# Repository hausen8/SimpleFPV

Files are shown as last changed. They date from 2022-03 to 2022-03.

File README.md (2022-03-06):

# SimpleFPV

If you need a low cost FPV drone that can be built by almost anyone, here it is.
This drone can be either 3D printed or simply cut from plywood. It was designed to carry a FPV camera and/or thermal camera like the FLIR Vue.

The drone can be equipped with almost any 7" or 8" motor/prop combination. If you have some old motors or ESCs, it is highly possible that you can use them. Flight controllers with a 30x30mm hole pattern are recommended but boxed controllers like the old DJI NAZA will fit, too. The battery size and voltage depends on the motors and motor controllers. Flight times up to 15 minutes with a lightweight cam are possible. Higher payload will reduce the flight time.

More information and documents will be added in the near future.

DIRECTORY                        | CONTENT
---------------------------------|----------------------------------------------------------
/3D-Print/                       | Directoy with all files for making the 3D printed version
/3D-Print/3D-Print_manual_XX.pdf | Manuals in different languages
/3D-Print/STL/                   | Sub directory containing all STL files
/3D-Print/3D-Print-N.png         | 3D Images of the drone
/Plywood/                        | Directoy with all files for making the plywood version
/Plywood/Plywood_manual_XX.pdf   | Manuals in different languages
/Plywood/Plywood-N.png           | 3D Images of the drone
/Plywood/Plywood-CNC.dxf         | CAD file for CNC milling or laser cutting the parts
/Plywood/Plywood-Parts.pdf       | PDF for printing contours on paper

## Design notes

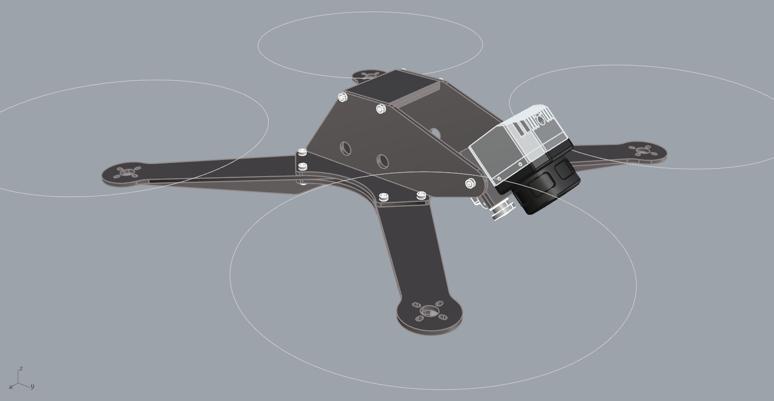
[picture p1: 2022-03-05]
Plywood/Plywood-1.png

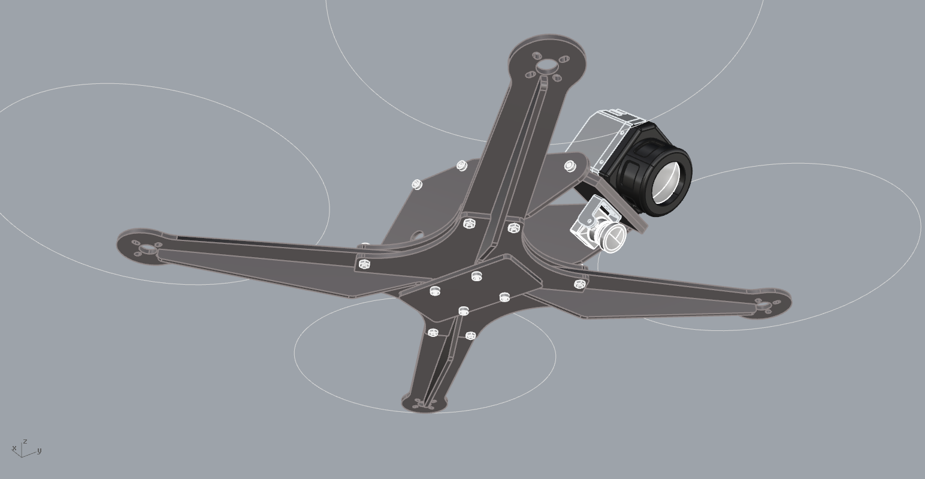
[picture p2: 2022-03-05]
Plywood/Plywood-2.png

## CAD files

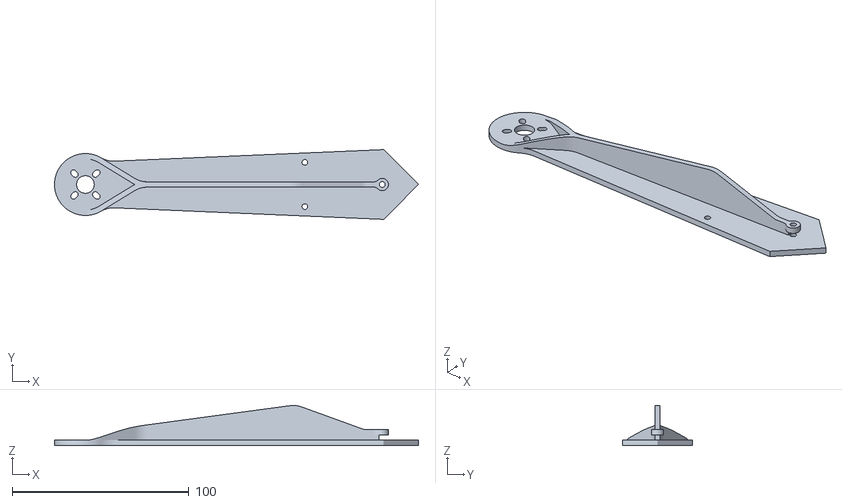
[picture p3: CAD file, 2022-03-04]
3D-Print/STL/Arm_2.stl
205.9 x 39.5 x 22.7

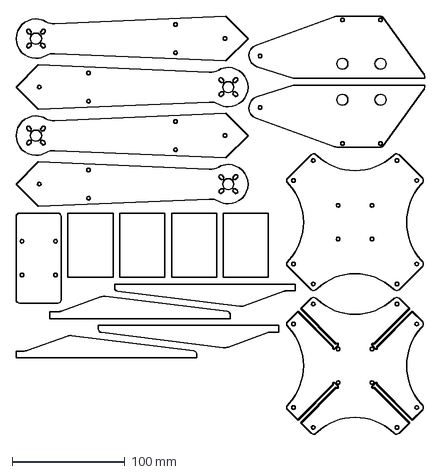
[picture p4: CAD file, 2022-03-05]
Plywood/Plywood-CNC.dxf
363.0 x 371.5 mm

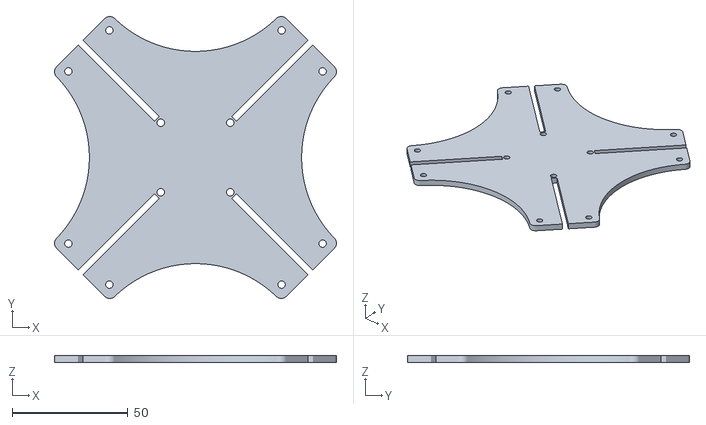
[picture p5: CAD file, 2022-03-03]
3D-Print/STL/CP_lower_2.stl
121.6 x 121.6 x 3.00

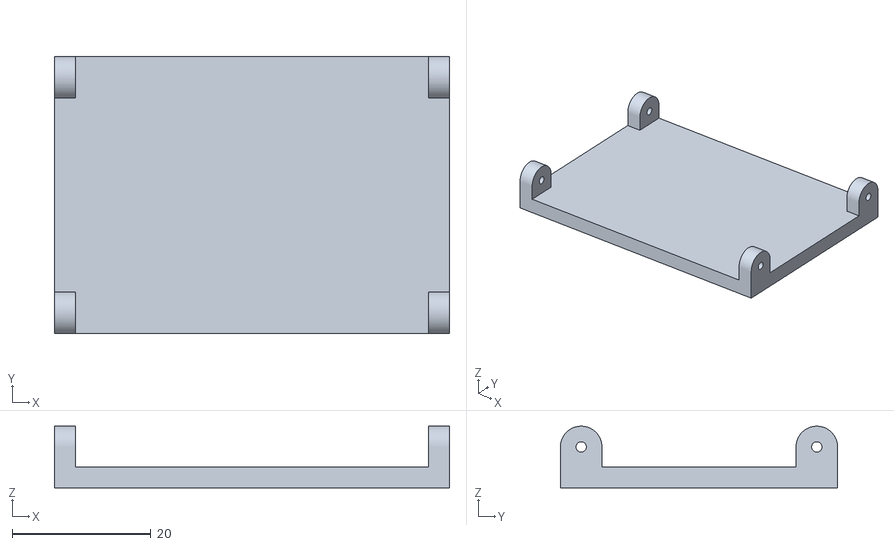
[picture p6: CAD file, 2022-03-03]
3D-Print/STL/VTX_plate.stl
57.0 x 40.0 x 8.90

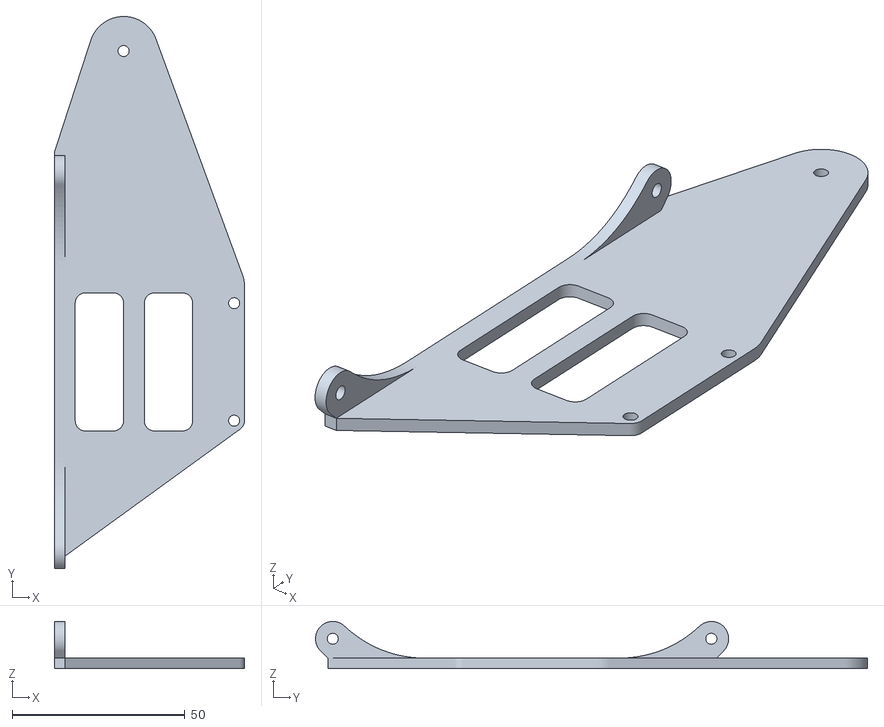
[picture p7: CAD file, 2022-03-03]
3D-Print/STL/Side_L.stl
55.0 x 159.8 x 13.6

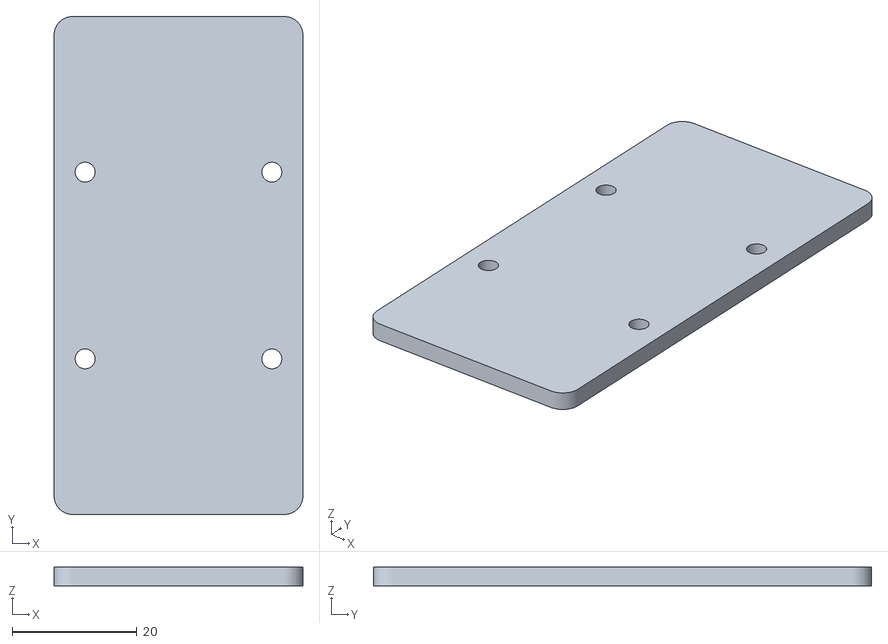
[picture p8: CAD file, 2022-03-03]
3D-Print/STL/BAT_plate.stl
40.0 x 80.0 x 3.00

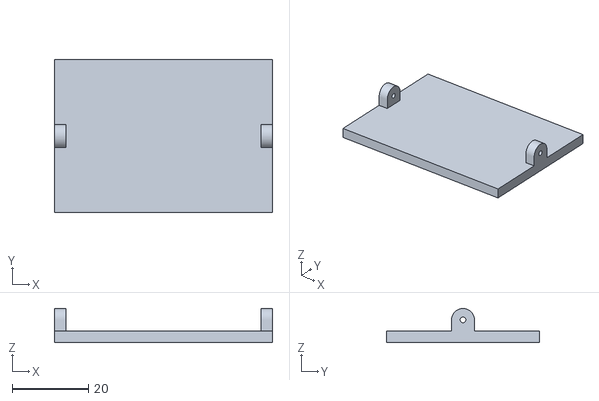
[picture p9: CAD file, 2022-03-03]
3D-Print/STL/CAM_plate.stl
57.0 x 40.0 x 8.90

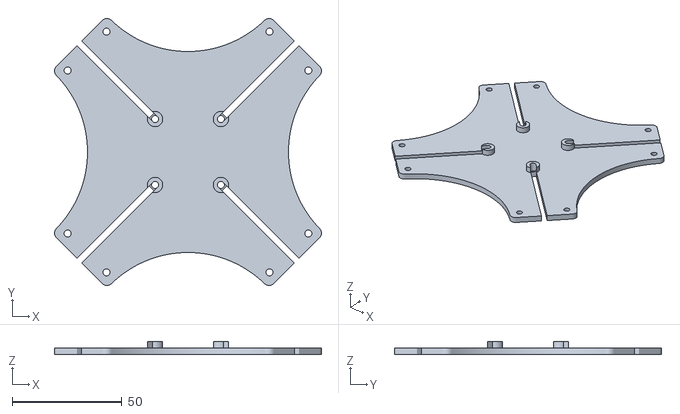
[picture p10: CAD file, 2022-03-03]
3D-Print/STL/CP_lower.stl
121.6 x 121.6 x 6.00

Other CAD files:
3D-Print/STL/Arm.stl
3D-Print/STL/Side_R.stl
3D-Print/STL/CP_upper.stl

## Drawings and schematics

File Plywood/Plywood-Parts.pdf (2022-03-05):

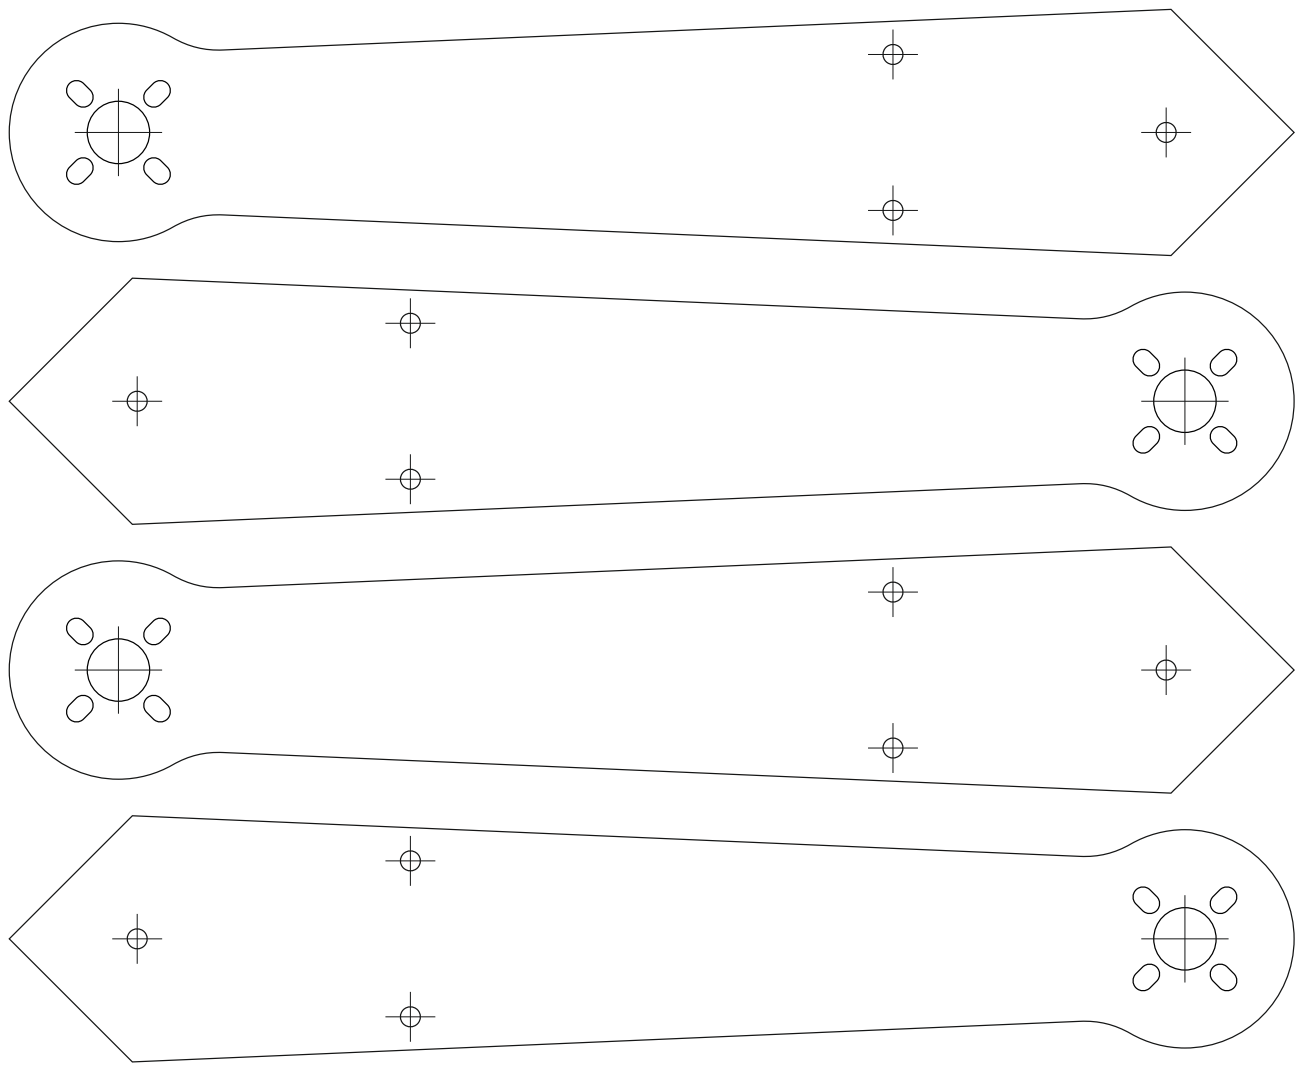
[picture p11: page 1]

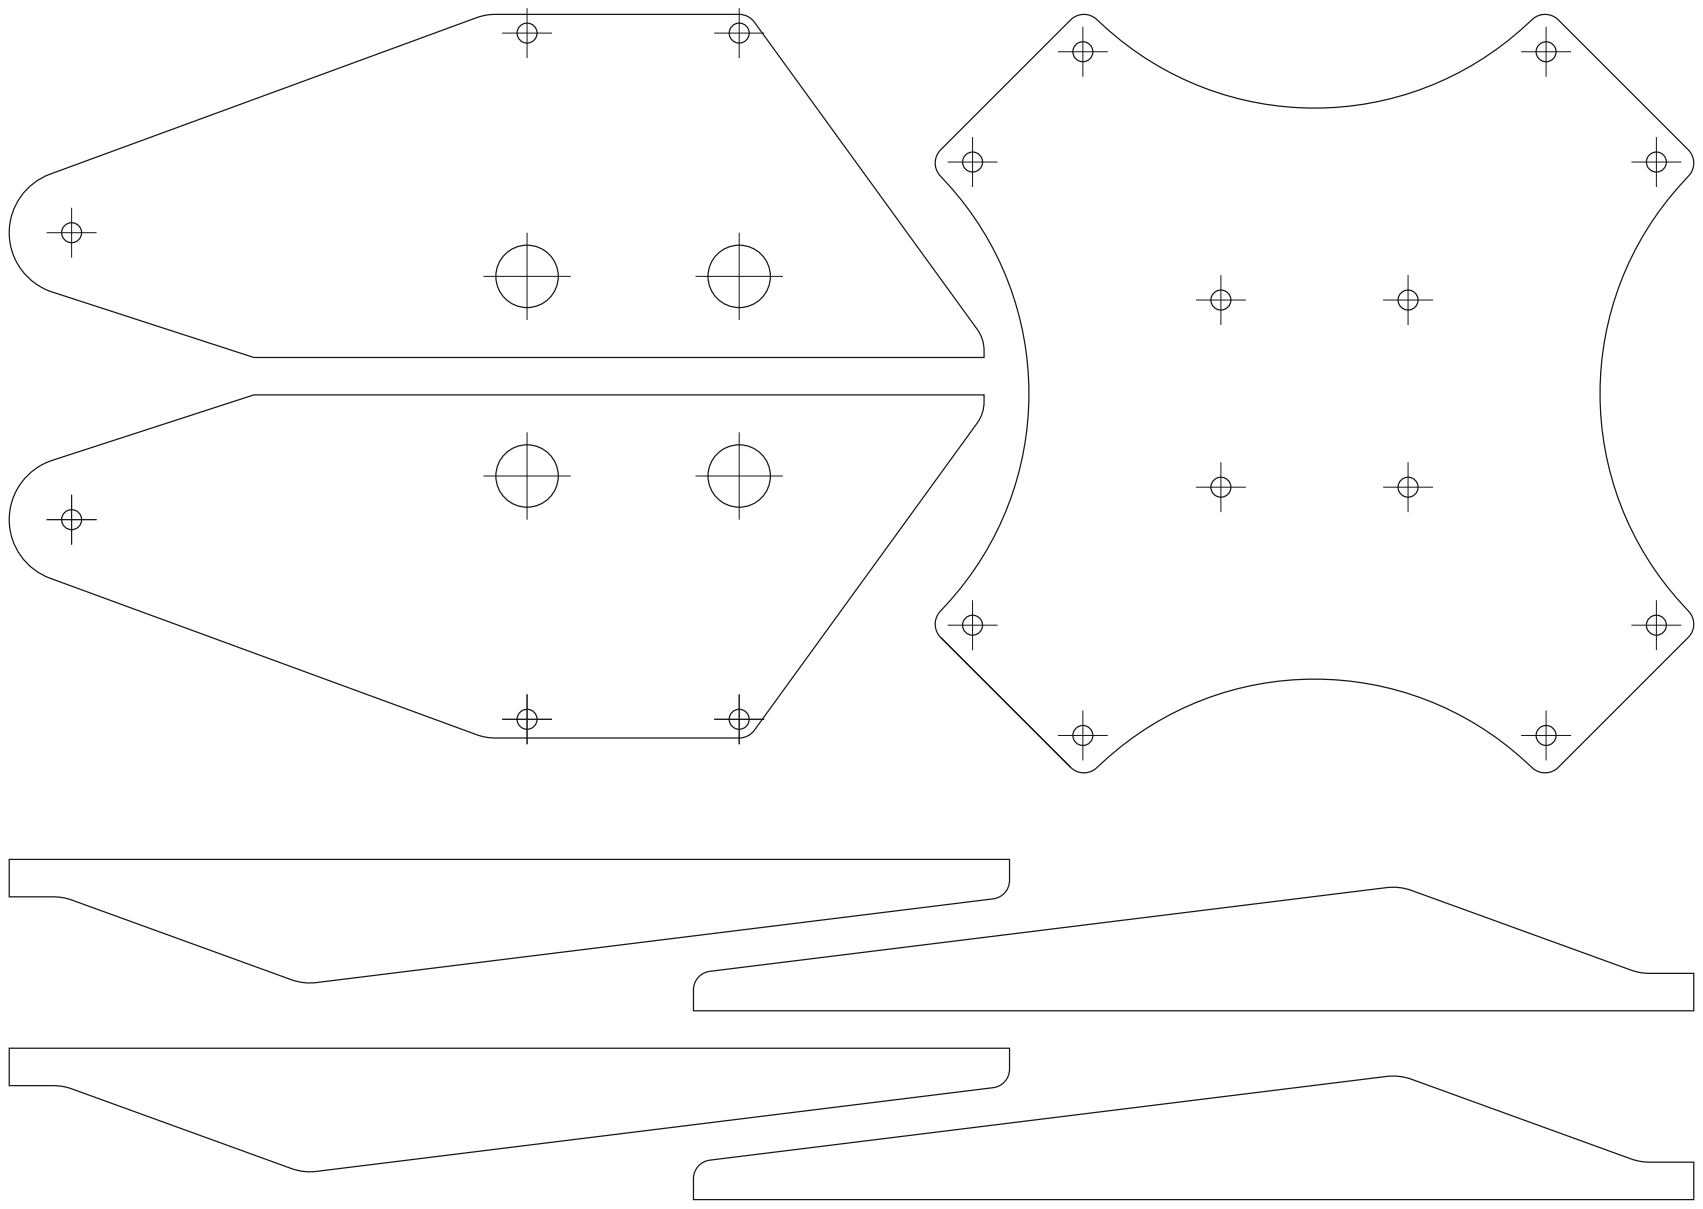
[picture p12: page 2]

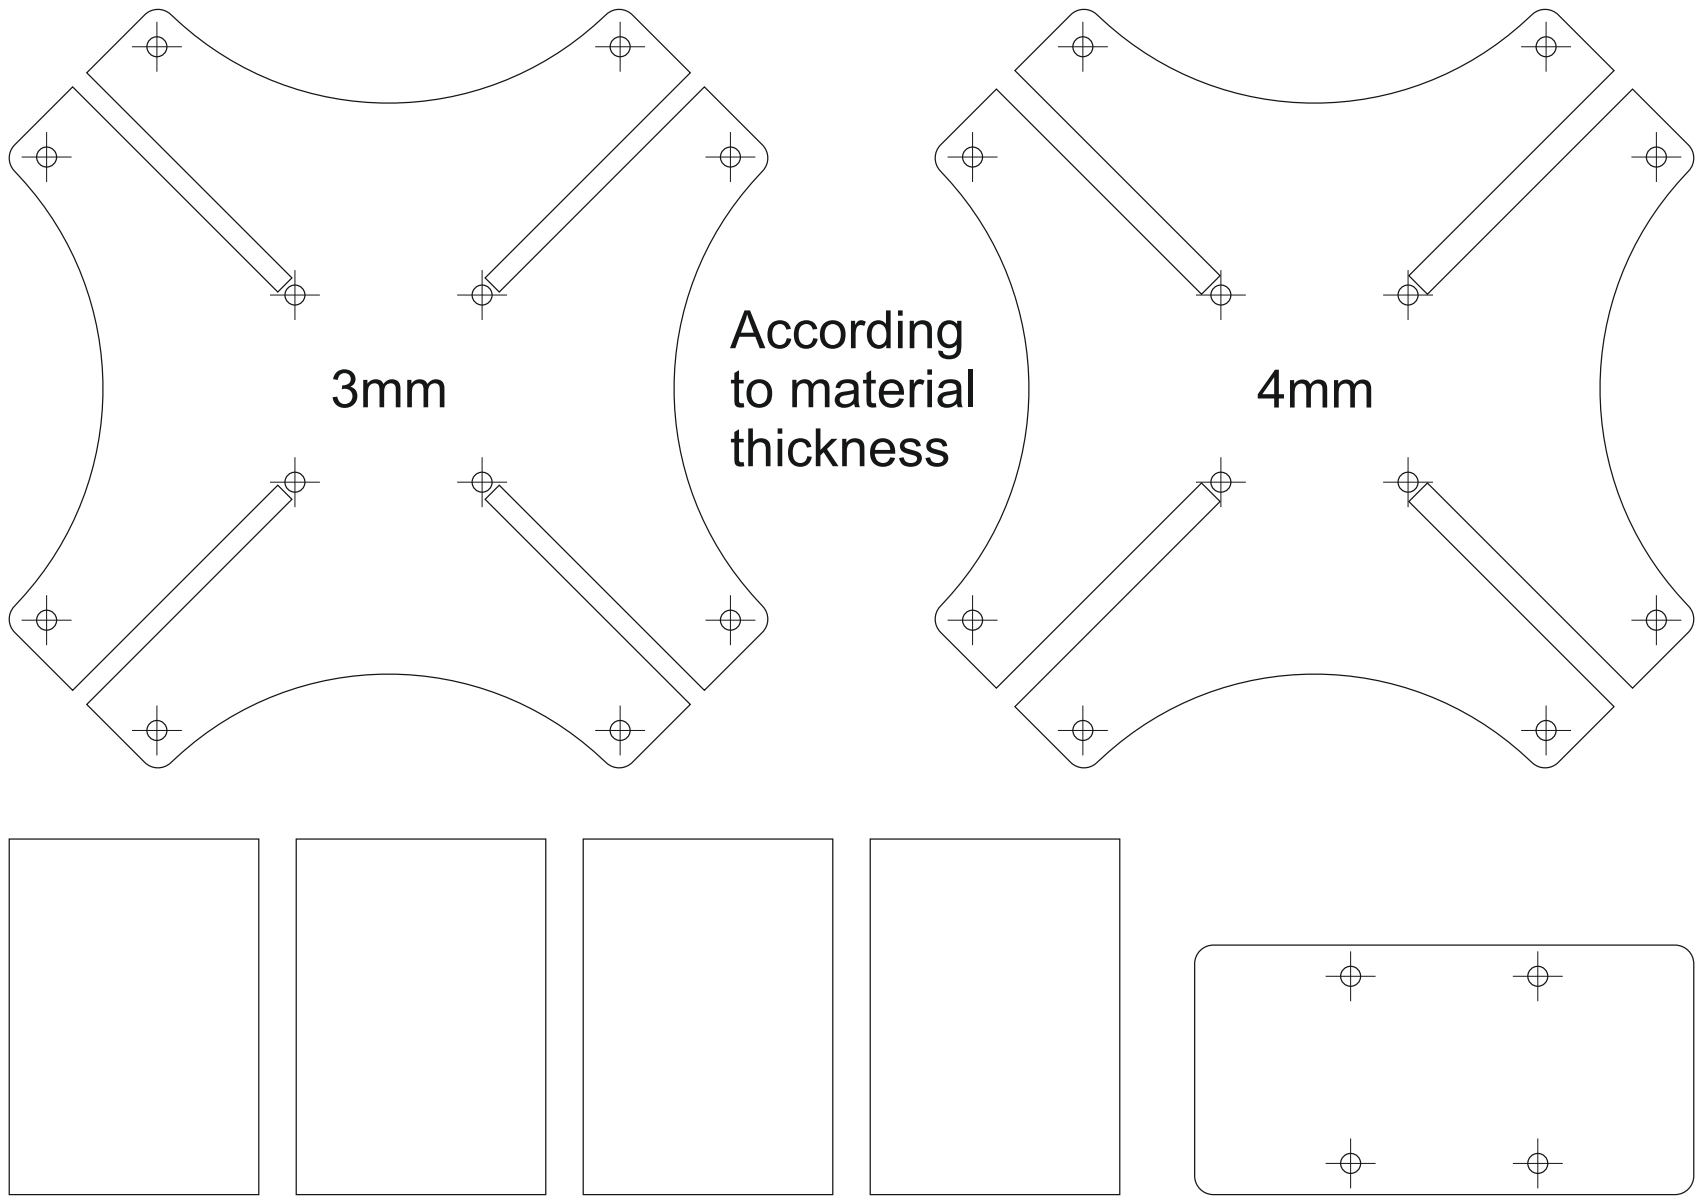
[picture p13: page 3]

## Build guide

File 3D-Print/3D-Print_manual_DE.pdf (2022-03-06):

3D-Druck:

Druck mit PLA: Top and bottom solid layers: 3, Outlines: 3, Infill honeycomb 20%
Bei den STL-Dateien besteht die Wahl zwischen zwei verschiedenen Armen:
- Arm_1.stl lässt sich wie alle anderen Teile ohne Support drucken, ergibt aber einen weniger steifen Rahmen. Diese Variante wird empfohlen, wenn keine besonderen Erfahrungen im 3D-Druck vorhanden sind.
- Arm_2.stl muss mit Support an der überhängenden Schraubenöse gedruckt werden. Nach dem Druck wird der Support entfernt. Diese Konstruktion führt zu einem steiferen Rahmen und richtet sich an erfahrenere Anwender.

Achtung: Zu jedem Arm gehört eine entsprechende untere Centerplate. Arm_1.stl ist nicht mit CP_lower_2.stl kompatibel und umgekehrt.

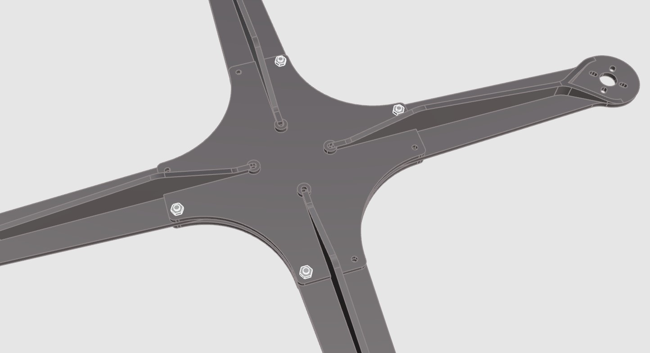
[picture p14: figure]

Schritt 1 (Arm_1):

Alle vier Arme mit je einer M3x15 Schraube an zwei gegenüberliegenden Seiten der oberen Centerplate fixieren. Anschließend die untere Centerplate auflegen und mit vier Muttern sichern.

Schritt 1 (Arm_2):

Einen Arm nach dem anderen zwischen die Centerplates schieben und mit je einer M3x15 Schraube und Mutter an zwei gegenüberliegenden Seiten sichern.

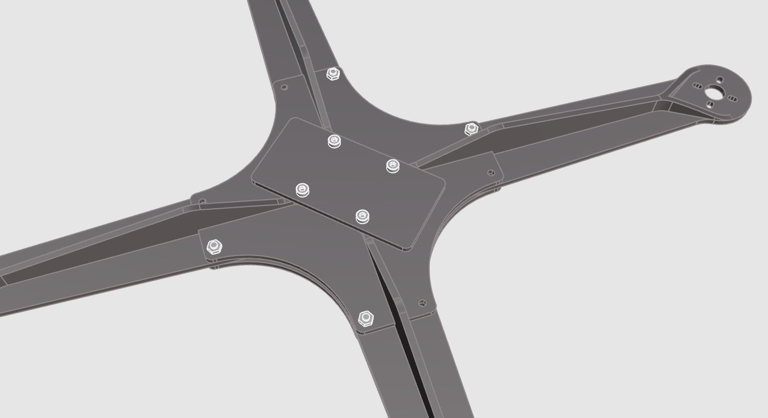
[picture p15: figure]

Schritt 2:

Den Akkuträger mit vier Schrauben M3x20 aufsetzen.

Schritt 3:

Auf der Gegenseite vier M3 Distanzbolzen auf die Schrauben aufsetzen und festziehen. Für die Elektronik steht eine Gesamthöhe von 49 Millimetern zur Verfügung. Bei mehreren elektronischen Boards sollten entsprechend kurze Distanzbolzen gewählt werden.

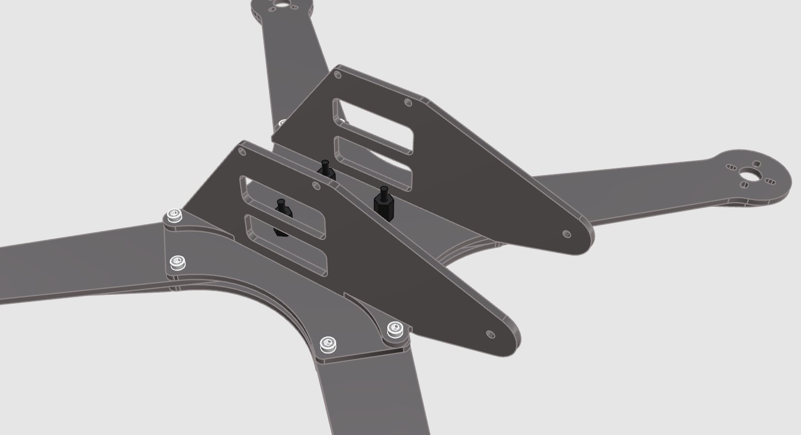
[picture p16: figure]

Schritt 4:

Seitenteile mit jeweils zwei M3x15 aufsetzen und auf der Rückseite mit Muttern sichern.

Schritt 5:

Die obere Trägerplatte kann wahlweise mit M3 Schrauben und Muttern oder aber mit Treibschrauben befestigt werden. Um M3 Schrauben zu verwenden, müssen die Bohrungen an der Trägerplatte auf 3mm aufgebohrt werden. Treibschrauben mit 2mm bis 2,6mm Durchmesser können ohne Aufbohren eingesetzt werden und schneiden sich ihr Gewinde selbst.

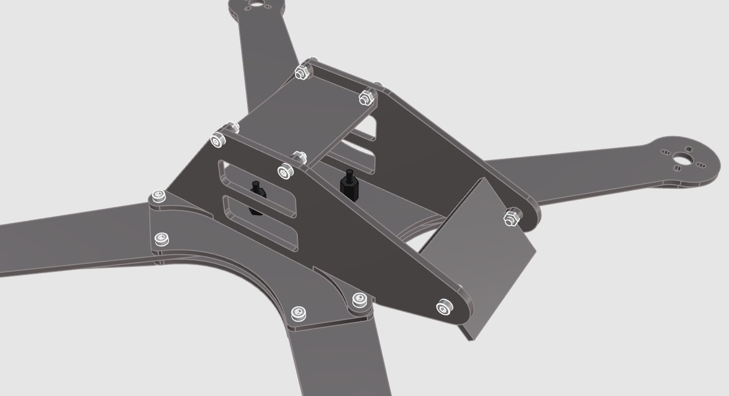
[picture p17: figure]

Schritt 6:

Auch die Trägerplatte für die Kameras kann wahlweise mit M3 Schrauben und Muttern oder mit Treibschrauben befestigt werden. Bei der Verwendung von M3 Schrauben müssen die Bohrungen des Trägers ebenfalls auf 3mm aufgebohrt werden. In diesem Fall sind Sicherungsmuttern empfohlen, damit sich der Träger mit der Kamera nicht während des Fluges verstellt.

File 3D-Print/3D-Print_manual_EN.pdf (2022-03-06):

3D Print:

Print with PLA: Top and bottom solid layers: 3, Outlines: 3, Infill honeycomb 20%
With the STL files there is a choice between two different arms:
- Arm_1.stl can be printed without support like all other parts, but results in a less rigid frame. This variant is recommended if you do not have any special experience in 3D printing.
- Arm_2.stl must be printed with support on the overhanging screw eyelet. After printing, the support is removed. This construction results in a stiffer frame and is aimed at more experienced users.

Note: Each arm has a corresponding lower center plate. Arm_1.stl is not compatible with CP_lower_2.stl and vice versa.


Step 1 (Arm_1):

Fix all four arms with one M3x15 screw each on two opposite sides of the upper center plate. Then place the lower center plate and secure with four nuts.

Step 1 (Arm_2):

Slide one arm at a time between the center plates and secure with an M3x15 screw and nut on two opposite sides.


Step 2:

Attach the battery carrier with four screws M3x20.

Step 3:

Place four M3 spacer bolts on the screws on the opposite side and tighten. A total height of 49 millimeters is available for the electronics. If there are several electronic boards, correspondingly short spacer bolts should be selected.


Step 4:

Put on the side parts with two M3x15 each and secure them with nuts on the back.

Step 5:

The upper support plate can be attached either with M3 screws and nuts or with self-tapping screws. In order to use M3 screws, the holes on the carrier plate must be drilled out to 3mm. Self-tapping screws with a diameter of 2mm to 2.6mm can be used without drilling and tap their own thread.


Step 6:

The support plate for the cameras can also be attached either with M3 screws and nuts or with self-tapping screws. When using M3 screws, the holes in the carrier must also be drilled out to 3mm. In this case, locking nuts are recommended to prevent the carrier with the camera from moving during flight.

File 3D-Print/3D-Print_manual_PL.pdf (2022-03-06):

Drukowanie 3D:

Drukowanie z PLA: Top and bottom solid layers: 3, Outlines: 3, Infill honeycomb 20%
W przypadku pilników STL mamy do wyboru dwa różne ramiona:
- Arm_1.stl można wydrukować bez wsparcia, jak wszystkie inne części, ale daje mniej sztywną ramkę. Ten wariant jest zalecany, jeśli nie masz specjalnego doświadczenia w druku 3D.
- Arm_2.stl musi być wydrukowany z podporą na zwisającym oczku śruby. Po wydrukowaniu podpora jest usuwana. Taka konstrukcja skutkuje sztywniejszą ramą i jest skierowana do bardziej doświadczonych użytkowników.

Uwaga: Każde ramię ma odpowiednią dolną płytę środkową. Arm_1.stl nie jest kompatybilny z CP_lower_2.stl i na odwrót.


Krok 1 (Ramię_1):

Zamocuj wszystkie cztery ramiona za pomocą jednej śruby M3x15 po dwóch przeciwnych stronach górnej płyty środkowej. Następnie umieść dolną płytę środkową i zabezpiecz czterema nakrętkami.

Krok 1 (Ramię_2):

Wsuń jedno ramię na raz między płyty środkowe i zabezpiecz śrubą M3x15 i nakrętką po dwóch przeciwnych stronach.


Krok 2:

Przymocuj nośnik baterii czterema śrubami M3x20.

Krok 3:

Umieść cztery śruby dystansowe M3 na śrubach po przeciwnej stronie i dokręć. Dla elektroniki dostępna jest całkowita wysokość 49 milimetrów. Z kilkoma elektronicznymi deskimi należy dobrać odpowiednie śruby dystansowe.


Krok 4:

Załóż boczne części po dwa M3x15 każda i zabezpiecz je nakrętkami z tyłu.

Krok 5:

Górną płytę nośną można przymocować za pomocą śrub i nakrętek M3 lub za pomocą wkrętów samogwintujących. Aby użyć śrub M3, otwory w płycie nośnej muszą być wywiercone do 3mm. Wkręty samogwintujące o średnicy od 2mm do 2,6mm można stosować bez wiercenia i gwintowania własnym gwintem.


Krok 6:

Płytę nośną dla kamer można również przymocować za pomocą śrub i nakrętek M3 lub wkrętów samogwintujących. W przypadku użycia śrub M3 otwory w nośniku muszą być również wywiercone do 3 mm. W takim przypadku zalecane są nakrętki blokujące, aby zapobiec przesuwaniu się nośnika z kamerą podczas lotu.

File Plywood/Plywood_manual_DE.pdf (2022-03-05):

Aussägen der Teile per Hand:

Drucke die Datei Plywood-Parts.pdf aus und klebe das Papier auf 4mm Sperrholz. Zur Not geht auch 3mm Sperrholz. Säge anschließend die Umrisse aus dem Sperrholz aus. Die untere Centerplate ist das einzige Teil, das sich nach Materialstärke unterscheidet. Es ist an den meisten Stellen keine besondere Präzision nötig. Auch die abgerundeten Ecken sind nicht wichtig.

CNC-gesteuertes Fräsen oder Laserschneiden:

Lade die Datei Plywood-CNC.dxf. Die Innen- und Außenkonturen sind jeweils auf einer eigenen Ebene abgelegt. Da sich die untere Centerplate für 3mm- oder 4mm-Sperrholz leicht unterscheidet, ist zu den Außenkonturen die Ebene mit der entsprechenden Centerplate auszuwählen.

Montage:

Die Arme können mit den beiden Centerplates wahlweise verschraubt oder verleimt werden. Eine Verleimung führt zu höherer Stabilität, verhindert aber die Möglichkeit einer späteren Reparatur. Wenn die Centerplates mit den Armen verleimt werden sollen, müssen die äußeren Schraubenlochpaare nicht gebohrt werden. Die inneren vier Bohrungen im 30x30mm Raster müssen in jedem Fall gebohrt werden.

Ein paar Bohrungen in den Seitenteilen des Aufbaus werden die spätere Verkabelung erleichtern.

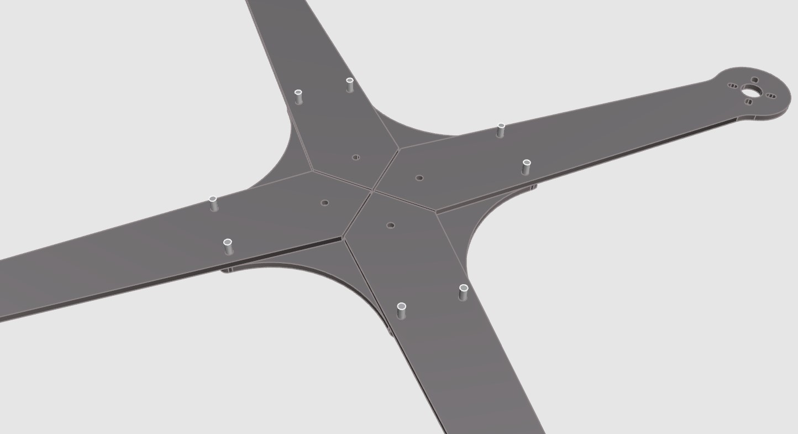
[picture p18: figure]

Schritt 1:

An den äußeren Enden M3x15 Schrauben durch die obere Centerplate und die vier Arme stecken. Alternativ können die Arme auch mit der Centerplate verleimt werden. Zwischen den Armen sollte ein Spalt von 1 Millimeter verbleiben.

Schritt 2:

Die untere Centerplate auflegen und mit M3 Muttern verschrauben. Zur besseren Ausrichtung sollten durch die vier inneren Bohrungen Schrauben gesteckt werden. Alternativ zur Verschraubung kann auch die untere Centerplate verleimt werden.

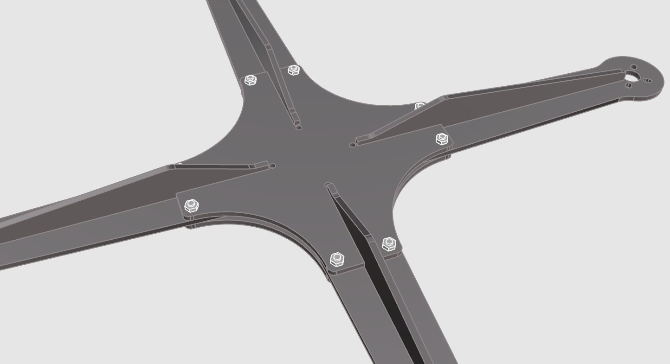
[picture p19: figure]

Schritt 3:

Die Schlitze der unteren Centerplate mit etwas Leim füllen. Die Auflageflächen der Versteifungen ebenfalls mit Leim bestreichen und auf die Arme aufleimen. Die Versteifungen dabei bis zum Anschlag in die Schlitze der unteren Centerplate drücken.

Schritt 4:

Akkuträger mit vier Schrauben M3x20 aufsetzen. Zur besseren Stabilität können die Auflageflächen auf den Versteifungen der Arme mit Leim bestrichen werden.

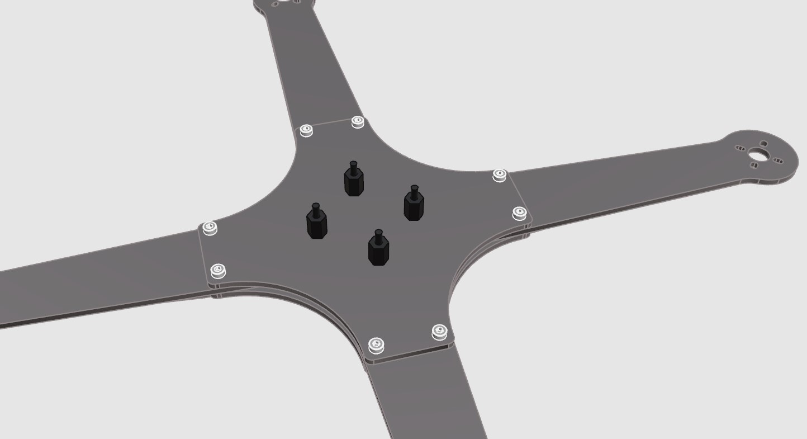
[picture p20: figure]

Schritt 5:

Auf der Gegenseite vier M3 Distanzbolzen auf die Schrauben aufsetzen und festziehen. Für die Elektronik steht eine Gesamthöhe von 49 Millimetern zur Verfügung. Bei mehreren elektronischen Boards sollten entsprechend kurze Distanzbolzen gewählt werden.

Schritt 6:

Zwei der vier 40x57mm Trägerplatten zusammenleimen und mit den beiden Seitenteilen verschrauben. Zum Verschrauben eignen sich Holzschrauben bis ca. 3mm, wobei zur Sicherheit vorgebohrt werden sollte. Ein Verleimen der Trägerplatte mit den Seitenteilen ist nicht empfehlenswert, da dadurch die Montage der Elektronik erschwert wird. Anschließend den Aufbau mit ausreichend Leim auf den Kontaktflächen auf die obere Centerplate aufsetzen und gerade in Flugrichtung ausrichten.

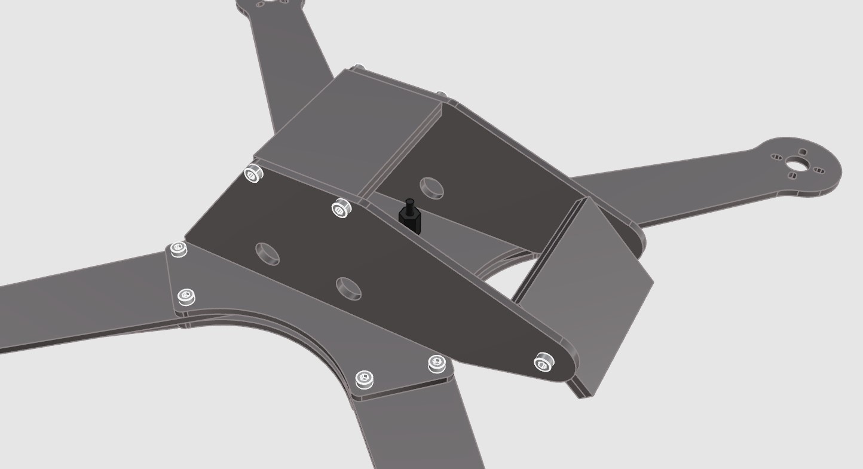
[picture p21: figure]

Schritt 7:

Die anderen beiden Trägerplatten ebenfalls miteinander verleimen. An den 40mm langen Kanten jeweils den Mittelpunkt markieren und vor dem Verschrauben vorbohren.

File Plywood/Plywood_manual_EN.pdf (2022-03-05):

Sawing out the parts by hand:

Print out the Plywood-Parts.pdf file and glue the paper onto 4mm plywood. In a pinch, 3mm plywood will do. Then saw the outlines out of the plywood. The lower center plate is the only part that differs in material thickness. No particular precision is required in most places. The rounded corners are also not important.

CNC controlled milling or laser cutting:

Load the Plywood-CNC.dxf file. The inner and outer contours are each stored on a separate layer. Since the lower center plate differs slightly for 3mm or 4mm plywood, the level with the corresponding center plate must be selected together with the outer contours.

Assembly:

The arms can either be screwed or glued to the two center plates. Gluing leads to greater stability, but prevents the possibility of later repairs. If the center plates are to be glued to the arms, the outer pairs of screw holes do not have to be drilled. The inner four holes in the 30x30mm grid must be drilled in any case.

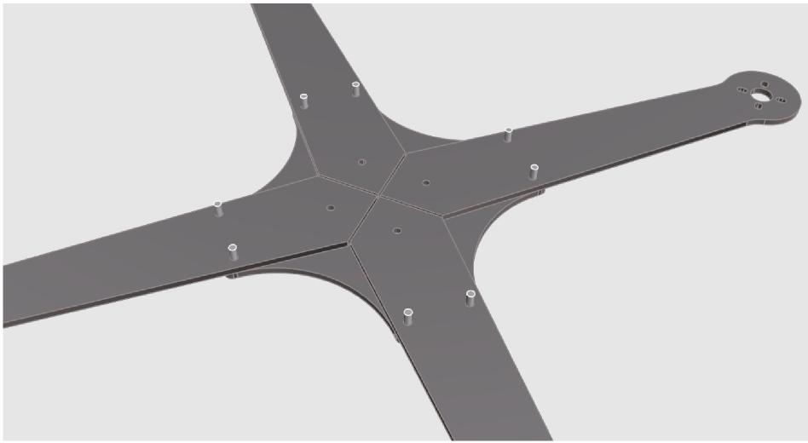
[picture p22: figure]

Step 1:

At the outer ends, insert M3x15 screws through the upper center plate and the four arms. Alternatively, the arms can also be glued to the center plate. A gap of 1 millimeter should remain between the arms.

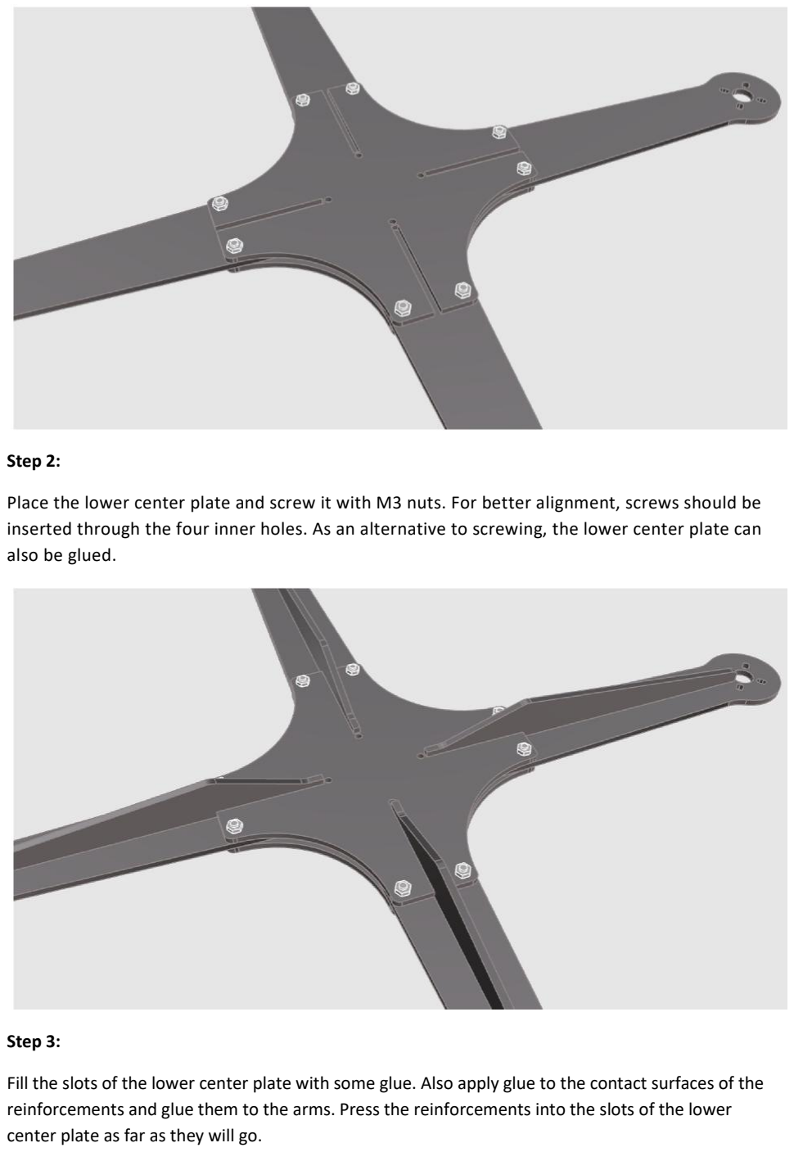
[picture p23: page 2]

Step 2:

Place the lower center plate and screw it with M3 nuts. For better alignment, screws should be inserted through the four inner holes. As an alternative to screwing, the lower center plate can also be glued.

Step 3:

Fill the slots of the lower center plate with some glue. Also apply glue to the contact surfaces of the reinforcements and glue them to the arms. Press the reinforcements into the slots of the lower center plate as far as they will go.

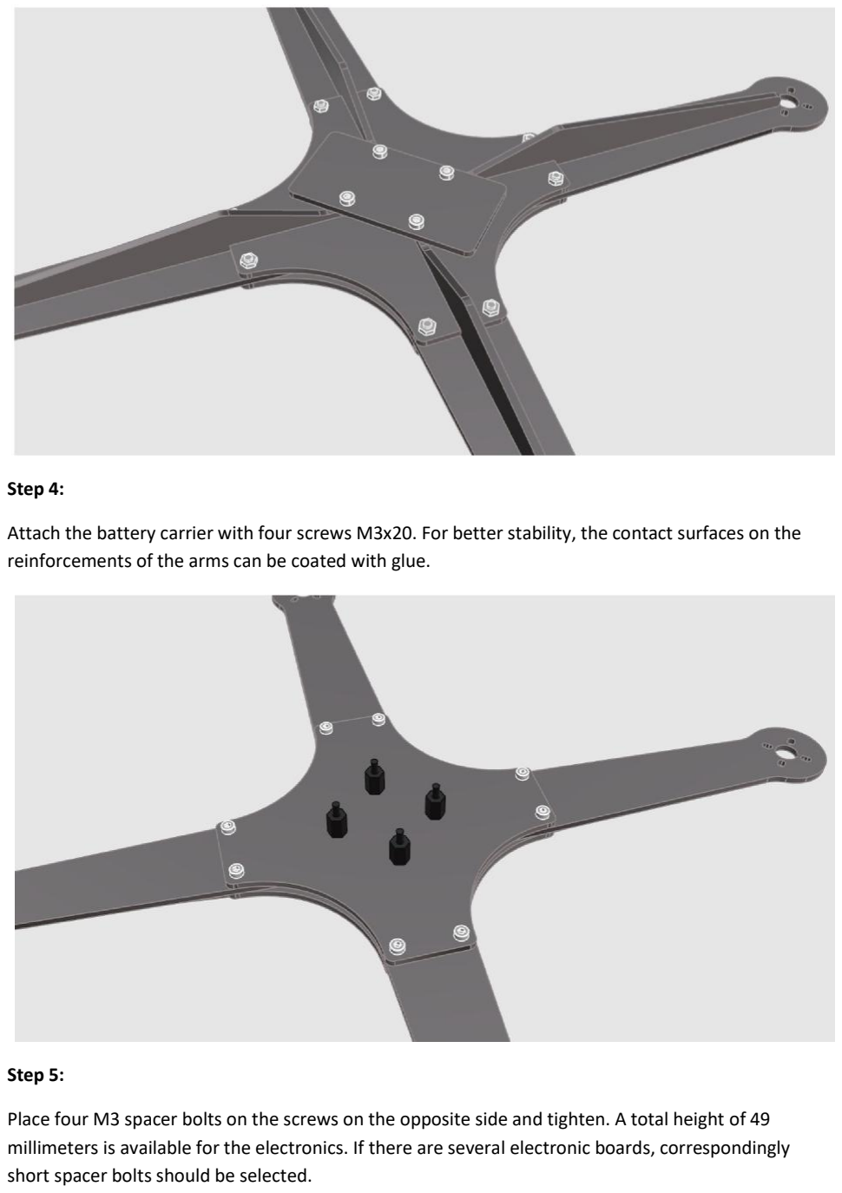
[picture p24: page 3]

Step 4:

Attach the battery carrier with four screws M3x20. For better stability, the contact surfaces on the reinforcements of the arms can be coated with glue.

Step 5:

Place four M3 spacer bolts on the screws on the opposite side and tighten. A total height of 49 millimeters is available for the electronics. If there are several electronic boards, correspondingly short spacer bolts should be selected.

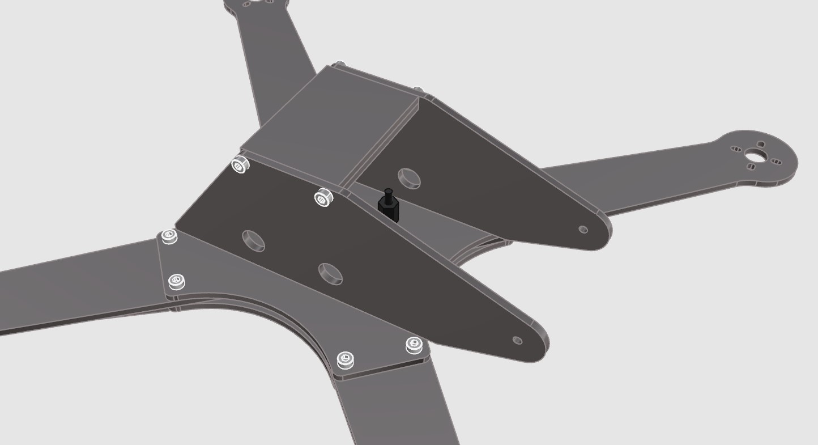
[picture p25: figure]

Step 6:

Glue two of the four 40x57mm carrier plates together and screw them to the two side panels. Wood screws up to approx. 3mm are suitable for screwing, whereby pre-drilling should be carried out to be on the safe side. Gluing the carrier plate to the side parts is not recommended, as this makes it difficult to assemble the electronics. Then place the structure on the upper center plate with sufficient glue on the contact surfaces and align it straight in the direction of flight.


Step 7:

Glue the other two carrier boards together as well. Mark the center point on each of the 40mm long edges and pre-drill before screwing

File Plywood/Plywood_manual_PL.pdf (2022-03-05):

Ręczne wycinanie części:

Wydrukuj plik Plywood-Parts.pdf i przyklej papier do sklejki 4mm. W mgnieniu oka wystarczy sklejka 3 mm. Potem wytnij kontury ze sklejki. Dolna płyta środkowa to jedyna część, która różni się grubością materiału. W większości miejsc nie jest wymagana żadna szczególna precyzja. Zaokrąglone rogi również nie są ważne.

Frezowanie sterowane CNC lub cięcie laserowe:

Załaduj plik Plywood-CNC.dxf. Każdy kontur wewnętrzny i zewnętrzny jest przechowywany na osobnej warstwie. Ponieważ dolna płyta środkowa różni się nieznacznie dla sklejki 3 mm lub 4 mm, poziom z odpowiednią płytą środkową należy wybrać dla zewnętrznych konturów.

Montaż:

Ramiona można przykręcić lub przykleić do dwóch płyt środkowych. Klejenie prowadzi do większej stabilności, ale zapobiega możliwości późniejszych napraw. Jeżeli płyty środkowe mają być przyklejone do ramion, zewnętrzne pary otworów na śruby nie muszą być wiercone. W każdym przypadku należy wywiercić cztery wewnętrzne otwory w siatce 30x30mm.


Krok 1:

Na zewnętrznych końcach włóż śruby M3x15 przez górną płytę środkową i cztery ramiona. Alternatywnie ramiona można również przykleić do płyty środkowej. Między ramionami powinien pozostać odstęp 1 milimetra.

Krok 2:

Umieść dolną płytę środkową i przykręć ją nakrętkami M3. Aby uzyskać lepsze wyrównanie, śruby należy włożyć przez cztery otwory wewnętrzne. Alternatywnie do przykręcania, dolną płytę środkową można również przykleić.


Krok 3:

Wypełnij szczeliny dolnej płyty środkowej odrobiną kleju. Klej należy również nałożyć na powierzchnie styku wzmocnień i przykleić je do ramion. Wciśnij wzmocnienia w szczeliny dolnej środkowej płyty do oporu.

Krok 4:

Przymocuj nośnik baterii czterema śrubami M3x20. Dla lepszej stabilności powierzchnie styku na wzmocnieniach ramion można pokryć klejem.


Krok 5:

Umieść cztery śruby dystansowe M3 na śrubach po przeciwnej stronie i dokręć. Dla elektroniki dostępna jest całkowita wysokość 49 milimetrów. W przypadku kilku płytek elektronicznych należy dobrać odpowiednio krótkie śruby dystansowe.

Krok 6:

Sklej ze sobą dwie z czterech płyt nośnych 40x57mm i przykręć je do dwóch paneli bocznych. Do wkręcania nadają się wkręty do drewna o średnicy do ok. 3 mm, przy czym dla bezpieczeństwa należy wykonać wstępne nawiercenie. Nie zaleca się przyklejania płyty nośnej do części bocznych, ponieważ utrudnia to montaż elektroniki. Następnie umieść konstrukcję na górnej płycie środkowej z wystarczającą ilością kleju na powierzchniach styku i wyrównaj ją prosto w kierunku lotu.


Krok 7:

Przyklej ze sobą również dwie pozostałe płyty nośne. Zaznacz punkt środkowy na każdej z 40-milimetrowych krawędzi i nawierć przed przykręceniem.

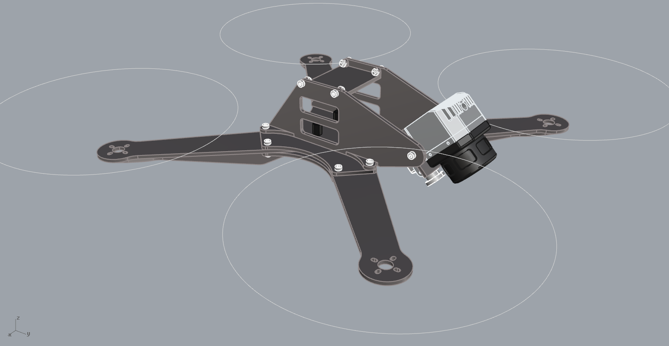
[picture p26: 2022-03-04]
3D-Print/3D-Print-1.png

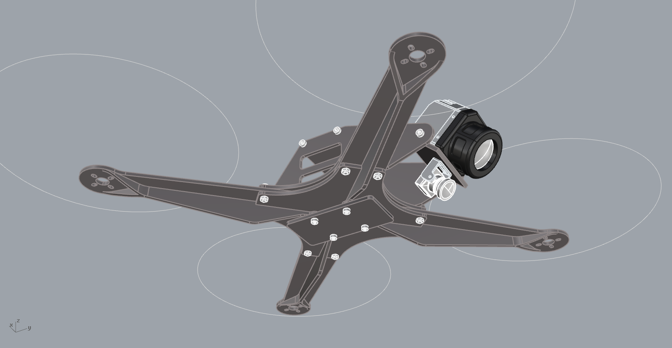
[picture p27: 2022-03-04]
3D-Print/3D-Print-2.png
